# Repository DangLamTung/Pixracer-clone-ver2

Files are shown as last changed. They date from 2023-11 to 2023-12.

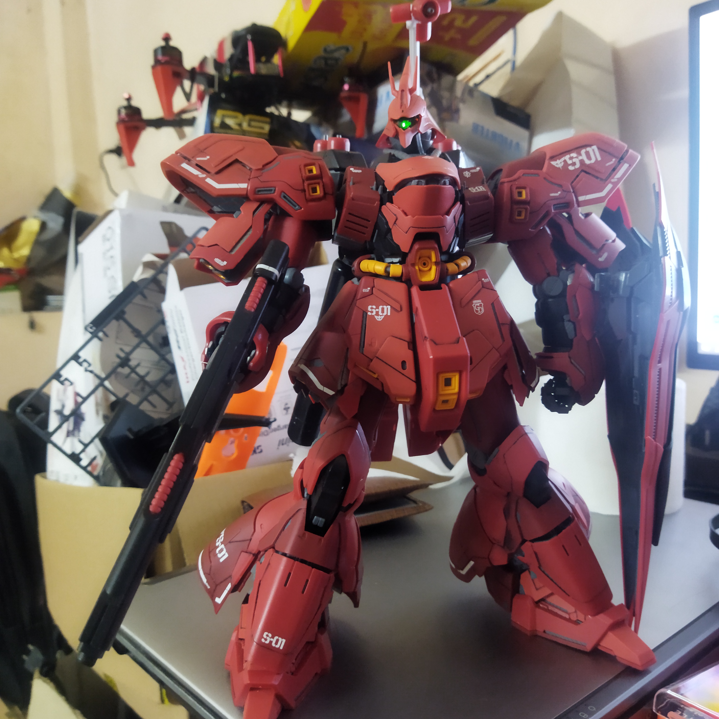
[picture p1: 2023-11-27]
IMG_20230711_230125.jpg

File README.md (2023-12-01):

# Pixracer_clone

 Open source flight controller based on the Pixracer flight controller.
 
 The  object of this project is to utilize the spare part I have :))) 
 
 The Flight controller using 36.5*36.5 FPV racing size, nowaday I think this is the most popular and flexible size for both FPV quadcopter and small-sized fixed wing.
 
 To make the soldering process easier, I used the smallest footprint is 0603, which can hand-solderable.
 
 This board will be mainly running Ardupilot firmware, but in the future I will test it with Betaflight and Inav
 
 This flight controller included these feature:
 

     +  STM32F429VIT6 microcontroller
     +  ICM20689 IMU 
     +  BMP280 barometer
     +  AT7456E OSD chip
     +  TPS5430 buck converter 5V output
     +  10 PWM outputs 
     +  5 UART, 2 I2C and 2 SPI pinout
     +  Built in voltage divider for battery monitoring
What can be improve?
     +  The original Pixracer dont have OSD chip for analog FPV, this may not be important in the future, because the development of recent digital FPV system, but I add a OSD anyway,
     +  The built in buck converter is 5V only, because of space constraint and to make the board atleast hand solderable, I didn't add a 9V buck, this is not ideal for using with 
     HD FPV system, I will add a 9V buck converter in the future.
     +  An ESP-32 or NRF52 wifi or bluetooth would be very nice to have in the next version :)))

Updaded the Inav  firmware and target

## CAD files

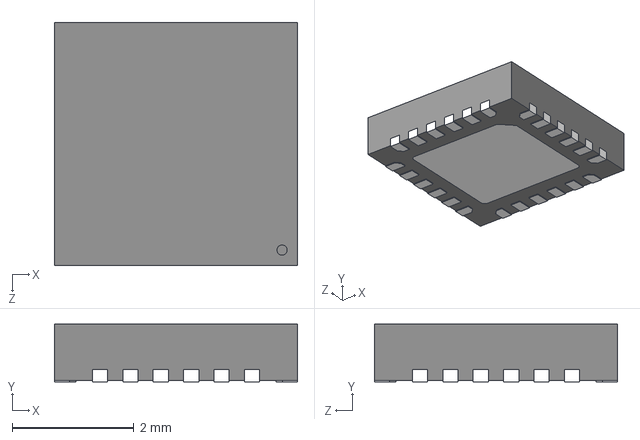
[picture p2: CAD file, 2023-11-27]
ICM-20689/ICM-20689.step
4.00 x 0.95 x 4.00 mm

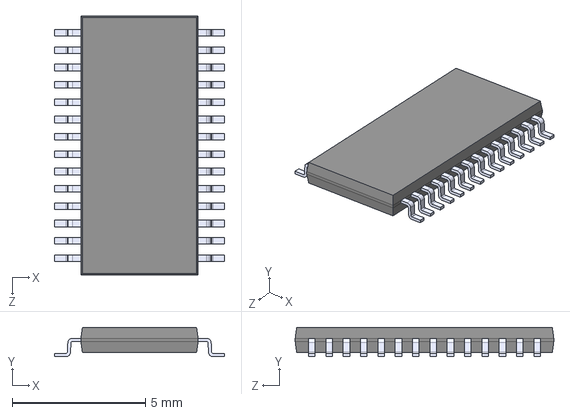
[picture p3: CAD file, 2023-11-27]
MAX7456EUI_/MAX7456EUI_.step
6.38 x 1.10 x 9.70 mm

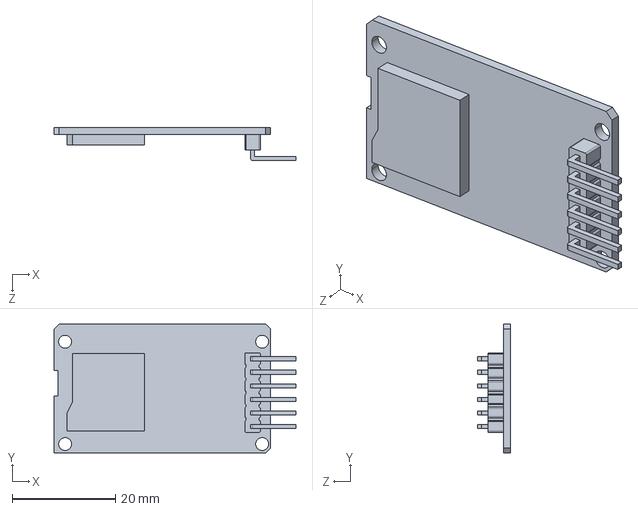
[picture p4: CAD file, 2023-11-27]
sdreader.STEP
46.9 x 25.0 x 6.40 mm

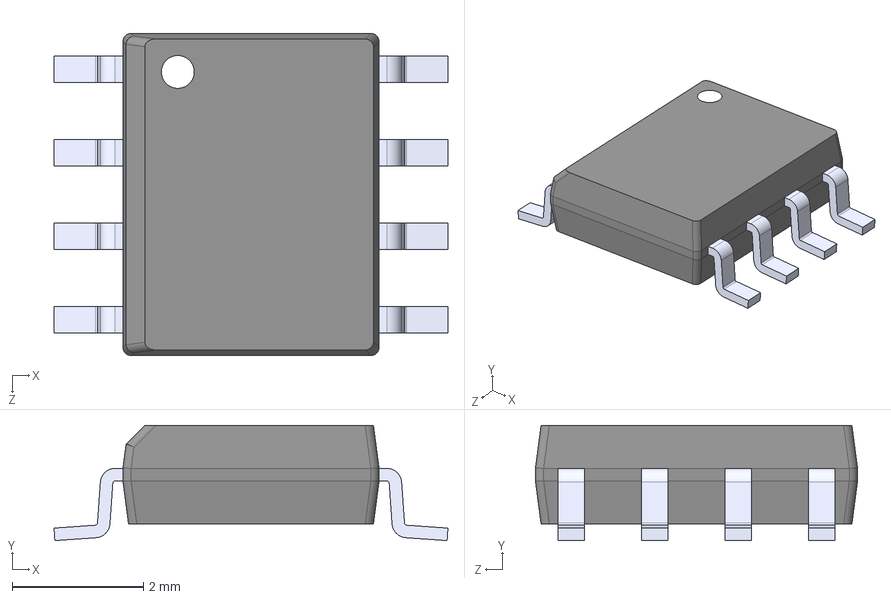
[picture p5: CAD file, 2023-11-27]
TPS54331D/TPS54331D.step
5.99 x 1.75 x 4.90 mm

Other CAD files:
sdreader.IGS
sdreader.SLDPRT

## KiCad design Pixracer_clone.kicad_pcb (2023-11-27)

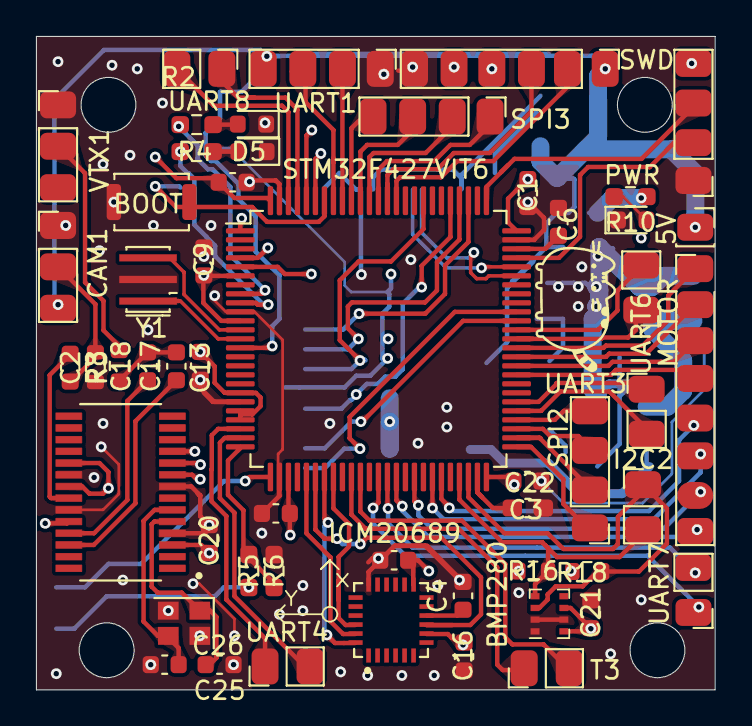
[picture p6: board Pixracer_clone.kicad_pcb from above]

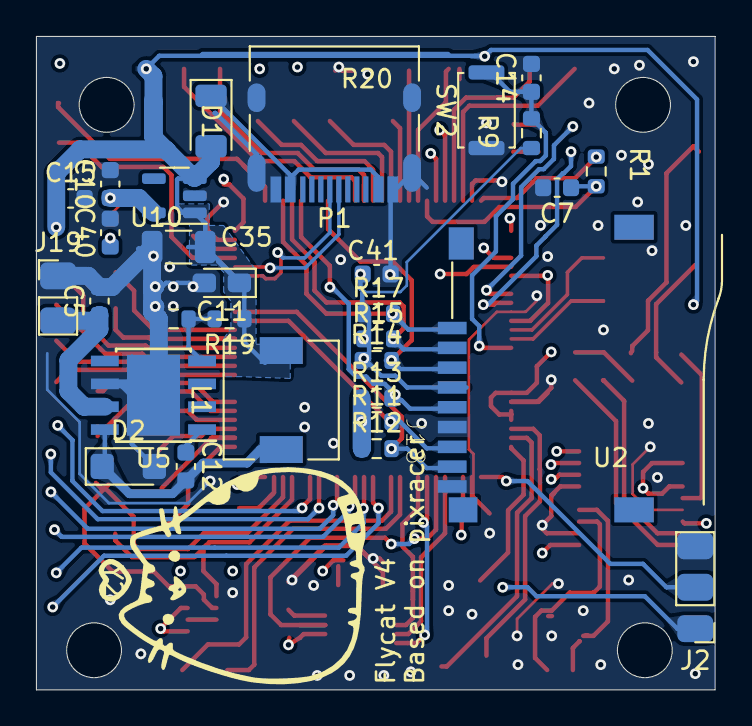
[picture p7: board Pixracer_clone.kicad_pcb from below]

Board: 4 copper layers, 37.7 x 36.3 mm, 83 parts (30 on the bottom side), 84 nets.

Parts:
5V: Conn_01x01_Pin; PinSocket_1x01_P2.00mm_Vertical
BMP280: BMP280; Bosch_LGA-8_2x2.5mm_P0.65mm_ClockwisePinNumbering
BOOT: SW_Push; SW_Push_SPST_NO_Alps_SKRK
C1: CP; C_0603_1608Metric
C2, C17, C25: 47uF; C_0603_1608Metric
C3: CP; C_0603_1608Metric_Pad1.08x0.95mm_HandSolder
C4, C16, C21, C23: 0.1uF; C_0603_1608Metric
C5, C6, C7, C8, C9, C13, C14, C19, C20, C22, C40: 100n; C_0603_1608Metric
C10: 1u; C_0603_1608Metric
C11: 220uF; CP_EIA-2012-15_AVX-P_Pad1.30x1.05mm_HandSolder
C12: 0.01uF; C_0603_1608Metric
C15, C41: C; C_0603_1608Metric
C18, C26: 22uF; C_0603_1608Metric
C35: CP; C_1206_3216Metric
CAM1: Conn_01x03_Male; PinHeader_1x03_P2.00mm_Vertical
D1: DIODE; D_1206_3216Metric
D2: B340; D_SMF
D4, D5: LED; LED_0603_1608Metric
GPS1: GPS; PinHeader_1x06_P2.00mm_Vertical
I2C2: Conn_01x02_Male; PinHeader_1x02_P2.00mm_Vertical
ICM20689: ICM-20689; QFN50P400X400X95-24N
J2: Conn_01x03_Pin; PinHeader_1x03_P2.00mm_Vertical
J18: Micro_SD_Card; SUNTECH_ST-TF-003A
J19: Conn_01x02_Pin; PinHeader_1x02_P2.00mm_Vertical
L1: 18uH; L_6.3x6.3_H3
MOTOR: Conn_01x08_Male; PinHeader_1x08_P2.00mm_Vertical
P1: USB_C_Plug_USB2.0; USB_C_Receptacle_HRO_TYPE-C-31-M-12
PWR: LED; LED_0603_1608Metric
R1, R9, R11, R12, R13, R14, R15, R16, R17, R18: R; R_0603_1608Metric
R2, R4, R10: R; R_0603_1608Metric_Pad0.98x0.95mm_HandSolder
R3, R8: 75R; R_0603_1608Metric
R5, R6: 10k; R_0603_1608Metric_Pad0.98x0.95mm_HandSolder
R19: 10kOhm; R_0603_1608Metric
R20: 3.24kOhm; R_0603_1608Metric
SPI2, SPI3: SPI3_Conn; PinHeader_1x04_P2.00mm_Vertical
STM32F427VIT6: STM32F427VITx; LQFP-100_14x14mm_P0.5mm
SW2: SW_Push; SW_Push_SPST_NO_Alps_SKRK
SWD: UART4_con; PinHeader_1x04_P2.00mm_Vertical
T3: Conn_01x02_Male; PinHeader_1x02_P2.00mm_Vertical
U2: MAX7456EUI+; SOP65P637X110-28N
U5: TPS5430DDA; TI_SO-PowerPAD-8_ThermalVias
U10: LP5907MFX-3.3; SOT-23-5
UART1: CRSF; PinHeader_1x04_P2.00mm_Vertical
UART3, UART4, UART6, UART7, UART8: Conn_01x02_Male; PinHeader_1x02_P2.00mm_Vertical
VTX1: Conn_01x03_Male; PinHeader_1x03_P2.00mm_Vertical
Y1: Resonator; Resonator_SMD_Murata_CSTxExxV-3Pin_3.0x1.1mm_HandSoldering
Y2: Crystal_GND24_Small; Crystal_SMD_2520-4Pin_2.5x2.0mm

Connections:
5V_IN: 5V.1, C11.1, C15.1, C35.1, CAM1.3, D1.2 (A), GPS1.1, L1.2, R19.1, U10.1 (IN), U10.3 (EN), UART1.4
BATT_CURRENT_SENSE: J2.2, STM32F427VIT6.26 (PA3)
BATT_VOLT: J2.1, R5.1
BATT_VOLT_SENSE: R5.2, R6.1, STM32F427VIT6.25 (PA2)
BOOT0: BOOT.2, C7.1, R1.2, STM32F427VIT6.94 (BOOT0)
GND: BMP280.1 (GND), BMP280.2 (CSB), BMP280.7 (GND), BOOT.1, C1.2, C3.2, C4.2, C5.2, C6.2, C7.2, C8.2, C9.2, C10.2, C11.2, C13.2, C14.2, C15.2, C16.2, C19.2, C20.2, C21.2, C22.2, C23.2, C25.1, C26.1, C35.2, C40.2, C41.2, CAM1.1, D2.2 (A), D4.1 (K), D5.1 (K), GPS1.6, ICM20689.18 (GND), J2.3, J18.6 (VSS), J18.9 (SHIELD), J19.1, P1.A1 (GND), P1.A12 (GND), P1.B1 (GND), P1.B12 (GND), P1.S1 (SHIELD), PWR.1 (K), R3.1, R6.2, R20.2, STM32F427VIT6.10 (VSS), STM32F427VIT6.20 (VSSA), STM32F427VIT6.27 (VSS), STM32F427VIT6.74 (VSS), STM32F427VIT6.99 (VSS), SW2.1, SWD.1, U2.4 (DGND), U2.8 (~CS), U2.20 (AGND), U2.23 (PGND), U5.6 (GND), U5.9 (GNDPAD), U10.2 (GND), UART1.1, VTX1.1, Y1.2, Y2.2, Y2.4
I2C2_SCl: BMP280.4 (SCK), I2C2.2, R16.2, STM32F427VIT6.47 (PB10)
I2C2_SDA: BMP280.3 (SDI), I2C2.1, R18.2, STM32F427VIT6.48 (PB11)
I2C_SCl: GPS1.4, STM32F427VIT6.95 (PB8)
I2C_SDA: GPS1.5, STM32F427VIT6.96 (PB9)
IMU_CLK: ICM20689.23 (SCL/SCLK), STM32F427VIT6.30 (PA5)
IMU_MISO: ICM20689.9 (AD0/SDO), STM32F427VIT6.31 (PA6)
IMU_MOSI: ICM20689.24 (SDA/SDI), STM32F427VIT6.32 (PA7)
LED2: R2.1, STM32F427VIT6.8 (PC14)
LED3: R4.1, STM32F427VIT6.9 (PC15)
MISO_OSD: STM32F427VIT6.4 (PE5), U2.11 (SDOUT)
MOSI_OSD: STM32F427VIT6.5 (PE6), U2.9 (SDIN)
MPU9250_CS: ICM20689.22 (NCS), STM32F427VIT6.33 (PC4)
NRST: C14.1, R9.2, STM32F427VIT6.14 (NRST), SW2.2
unnamed: C17.2, C18.2, R8.1
unnamed: C12.2, D2.1 (K), L1.1, U5.8 (PH)
unnamed: D4.2 (A), R2.2
unnamed: D5.2 (A), R4.2
unnamed: PWR.2 (A), R10.2
unnamed: C4.1, ICM20689.10 (REGOUT)
unnamed: C25.2, U2.5 (CLKIN), Y2.1
unnamed: C18.1, U2.25 (SAG)
unnamed: C2.2, U2.22 (VIN)
unnamed: C17.1, U2.26 (VOUT)
unnamed: C26.2, U2.6 (XFB), Y2.3
unnamed: C12.1, U5.1 (BOOT)
unnamed: R19.2, R20.1, U5.4 (VSENSE)
OSC1+: STM32F427VIT6.12 (PH0), Y1.3
OSC1-: STM32F427VIT6.13 (PH1), Y1.1
OSD_VIDEO_IN: C2.1, CAM1.2, R3.2
OSD_VIDEO_OUT: R8.2, VTX1.2
PWR_IN: C5.1, J19.2, U5.7 (VIN), VTX1.3
SBUS: STM32F427VIT6.24 (PA1), UART4.2
SCLK_OSD: STM32F427VIT6.1 (PE2), U2.10 (SCLK)
SDIO0: J18.7 (DAT0), R11.2, STM32F427VIT6.65 (PC8)
SDIO1: J18.8 (DAT1), R12.2, STM32F427VIT6.66 (PC9)
SDIO2: J18.1 (DAT2), R17.2, STM32F427VIT6.78 (PC10)
SDIO3: J18.2 (DAT3/CD), R15.2, STM32F427VIT6.79 (PC11)
SDIO_CLK: J18.5 (CLK), R13.2, STM32F427VIT6.80 (PC12)
SDIO_CMD: J18.3 (CMD), R14.2, STM32F427VIT6.83 (PD2)
SPI2_CS: SPI2.1, STM32F427VIT6.51 (PB12)
SPI2_MISO: SPI2.3, STM32F427VIT6.53 (PB14)
SPI2_MOSI: SPI2.4, STM32F427VIT6.54 (PB15)
SPI2_SCK: SPI2.2, STM32F427VIT6.52 (PB13)
SPI3_CS: SPI3.1, STM32F427VIT6.88 (PD7)
SPI3_MISO: SPI3.3, STM32F427VIT6.90 (PB4)
SPI3_MOSI: SPI3.4, STM32F427VIT6.91 (PB5)
SPI3_SCK: SPI3.2, STM32F427VIT6.89 (PB3)
SWCLK: STM32F427VIT6.76 (PA14), SWD.3
SWDIO: STM32F427VIT6.72 (PA13), SWD.2
TIM1_CH1: MOTOR.8, STM32F427VIT6.40 (PE9)
TIM1_CH2: MOTOR.7, STM32F427VIT6.42 (PE11)
TIM1_CH3: MOTOR.6, STM32F427VIT6.44 (PE13)
TIM1_CH4: MOTOR.5, STM32F427VIT6.45 (PE14)
TIM3_CH3: STM32F427VIT6.35 (PB0), T3.1
TIM3_CH4: STM32F427VIT6.36 (PB1), T3.2
TIM4_CH1: MOTOR.4, STM32F427VIT6.59 (PD12)
TIM4_CH2: MOTOR.3, STM32F427VIT6.60 (PD13)
TIM4_CH3: MOTOR.2, STM32F427VIT6.61 (PD14)
TIM4_CH4: MOTOR.1, STM32F427VIT6.62 (PD15)
UART1_RX: STM32F427VIT6.93 (PB7), UART1.3
UART1_TX: STM32F427VIT6.92 (PB6), UART1.2
UART2_RX: GPS1.3, STM32F427VIT6.87 (PD6)
UART2_TX: GPS1.2, STM32F427VIT6.86 (PD5)
UART3_RX: STM32F427VIT6.55 (PD8), UART3.2
UART3_TX: STM32F427VIT6.56 (PD9), UART3.1
UART4_TX: STM32F427VIT6.23 (PA0), UART4.1
UART6_RX: STM32F427VIT6.64 (PC7), UART6.2
UART6_TX: STM32F427VIT6.63 (PC6), UART6.1
UART7_RX: STM32F427VIT6.38 (PE7), UART7.1
UART7_TX: STM32F427VIT6.39 (PE8), UART7.2
UART8_RX: STM32F427VIT6.97 (PE0), UART8.1
UART8_TX: STM32F427VIT6.98 (PE1), UART8.2
USB_D+: P1.A6 (D+), STM32F427VIT6.71 (PA12)
USB_D-: P1.A7 (D-), STM32F427VIT6.70 (PA11)
VBUS: D1.1 (K), P1.A4 (VBUS), P1.A9 (VBUS), P1.B4 (VBUS), P1.B9 (VBUS)
VCAP_1: C3.1, STM32F427VIT6.49 (VCAP_1)
VCAP_2: C1.1, STM32F427VIT6.73 (VCAP_2)
VCC: BMP280.6 (VDDIO), BMP280.8 (VDD), C6.1, C8.1, C9.1, C10.1, C13.1, C16.1, C19.1, C20.1, C21.1, C22.1, C23.1, C40.1, C41.1, ICM20689.8 (VDDIO), ICM20689.13 (VDD), J18.4 (VDD), R1.1, R9.1, R10.1, R11.1, R12.1, R13.1, R14.1, R15.1, R16.1, R17.1, R18.1, STM32F427VIT6.6 (VBAT), STM32F427VIT6.11 (VDD), STM32F427VIT6.19 (VDD), STM32F427VIT6.21 (VREF+), STM32F427VIT6.22 (VDDA), STM32F427VIT6.28 (VDD), STM32F427VIT6.50 (VDD), STM32F427VIT6.75 (VDD), STM32F427VIT6.100 (VDD), SWD.4, U2.3 (DVDD), U2.19 (~RESET), U2.21 (AVDD), U2.24 (PVDD), U10.5 (OUT)

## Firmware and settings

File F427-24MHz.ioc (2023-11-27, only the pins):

Mcu.UserName=STM32F427VITx
PA0/WKUP.Signal=UART4_TX
PA1.Signal=UART4_RX
PA10.Signal=USART1_RX
PA11.Signal=USB_OTG_FS_DM
PA12.Signal=USB_OTG_FS_DP
PA13.Signal=SYS_JTMS-SWDIO
PA14.Signal=SYS_JTCK-SWCLK
PA2.Signal=ADCx_IN2
PA3.Signal=ADCx_IN3
PA4.Signal=ADCx_IN4
PA5.Signal=SPI1_SCK
PA6.Signal=SPI1_MISO
PA7.Signal=SPI1_MOSI
PA8.Signal=RCC_MCO_1
PA9.Signal=USART1_TX
PB0.Signal=GPIO_Output
PB1.Signal=GPIO_Output
PB10.Signal=I2C2_SCL
PB11.Signal=I2C2_SDA
PB12.Signal=GPIO_Output
PB13.Signal=SPI2_SCK
PB14.Signal=SPI2_MISO
PB15.Signal=SPI2_MOSI
PB2/BOOT1.Signal=GPIO_Output
PB3.Signal=SPI3_SCK
PB4.Signal=SPI3_MISO
PB5.Signal=SPI3_MOSI
PB6.Signal=I2C1_SCL
PB7.Signal=I2C1_SDA
PC10.Signal=SDIO_D2
PC11.Signal=SDIO_D3
PC12.Signal=SDIO_CK
PC4.Signal=GPIO_Output
PC5.Signal=GPIO_Output
PC6.Signal=USART6_TX
PC7.Signal=USART6_RX
PC8.Signal=SDIO_D0
PC9.Signal=SDIO_D1
PD0.Signal=CAN1_RX
PD1.Signal=CAN1_TX
PD12.Signal=S_TIM4_CH1
PD13.Signal=S_TIM4_CH2
PD14.Signal=S_TIM4_CH3
PD15.Signal=S_TIM4_CH4
PD2.Signal=SDIO_CMD
PD3.Signal=USART2_CTS
PD4.Signal=USART2_RTS
PD5.Signal=USART2_TX
PD6.Signal=USART2_RX
PD8.Signal=USART3_TX
PD9.Signal=USART3_RX
PE0.Signal=UART8_RX
PE1.Signal=UART8_TX
PE11.Signal=S_TIM1_CH2
PE13.Signal=S_TIM1_CH3
PE14.Signal=S_TIM1_CH4
PE2.Signal=SPI4_SCK
PE5.Signal=SPI4_MISO
PE6.Signal=SPI4_MOSI
PE7.Signal=UART7_RX
PE8.Signal=UART7_TX
PE9.Signal=S_TIM1_CH1
PH0/OSC_IN.Signal=RCC_OSC_IN
PH1/OSC_OUT.Signal=RCC_OSC_OUT
